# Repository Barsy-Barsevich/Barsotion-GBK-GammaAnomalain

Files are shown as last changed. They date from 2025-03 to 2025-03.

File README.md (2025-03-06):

# Barsotion GBK GammaAnomalain

Board computer created for "OKB Iva "Kilka"", 2024

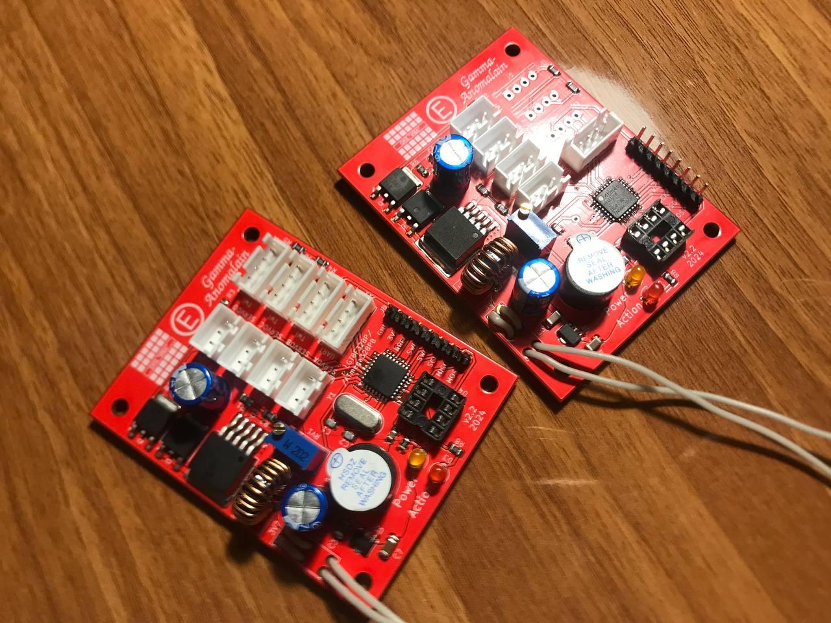
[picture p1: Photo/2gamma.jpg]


## Parameters
- Microcontroller: ATmega328PB / LGT8X328P
- Clock frequency: 16MHz / 32MHz
- Gyroscope: external, MPU6050 (I2C)
- Barometer: external, 2x BMP388 (I2C)
- Memory: 8MB SPI NOR Flash

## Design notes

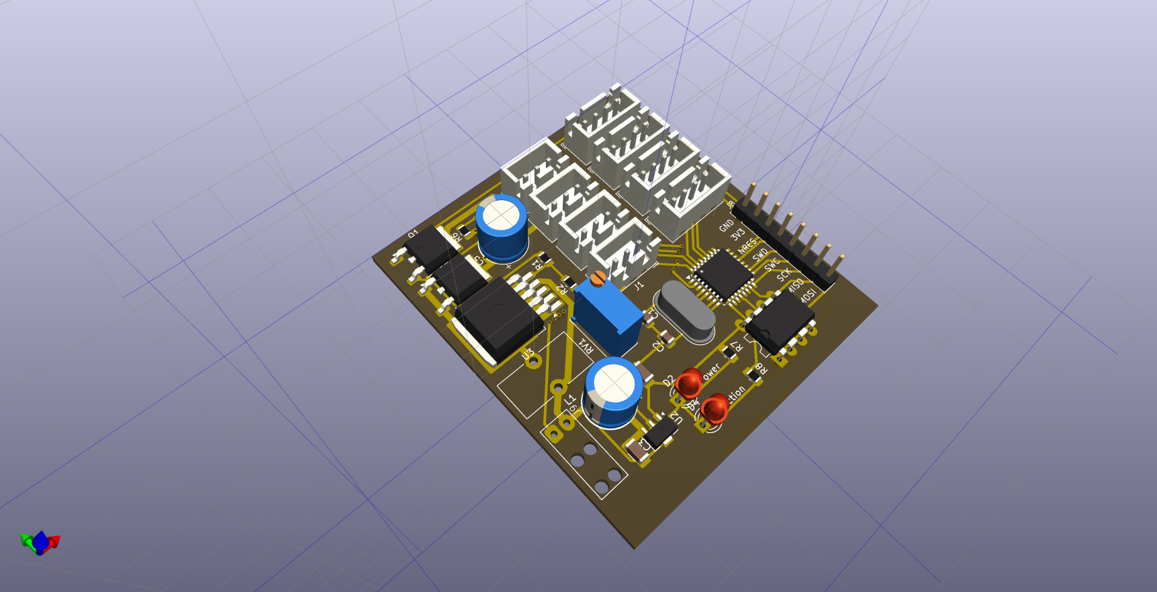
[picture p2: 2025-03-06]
Photo/GammaAnomalain.png

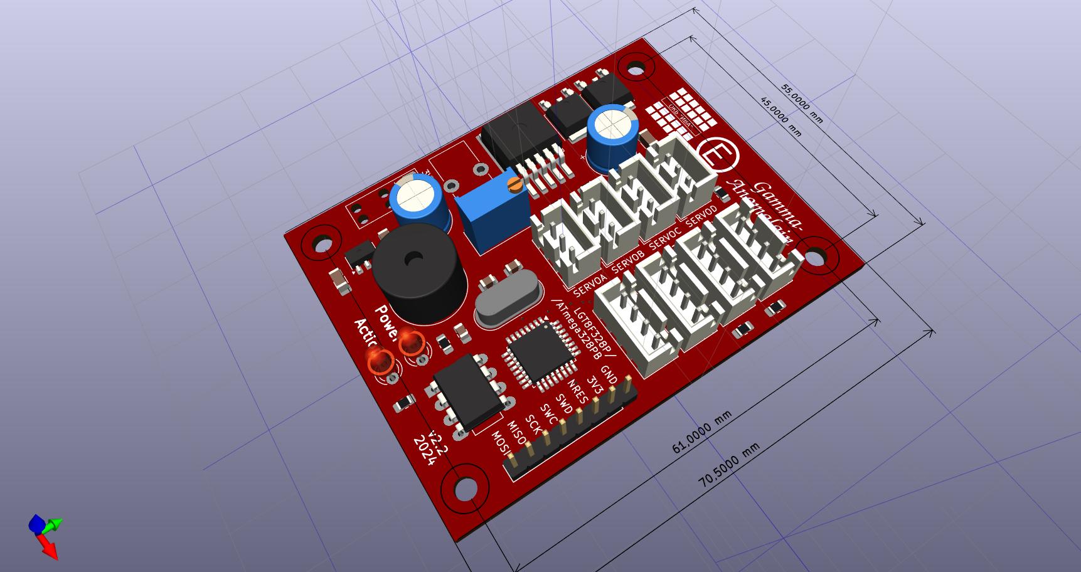
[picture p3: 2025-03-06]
Photo/GammaAnomalain_v2.2_3Dview_RedMask.jpg

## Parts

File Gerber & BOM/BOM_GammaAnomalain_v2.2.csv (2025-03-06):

Reference | Value | Footprint | Description
BZ1 | Buzzer | Buzzer_Beeper:MagneticBuzzer_ProSignal_ABI-009-RC | Buzzer, polarized
C1 | 22pF | Capacitor_SMD:C_0805_2012Metric | Unpolarized capacitor
C2 | 22pF | Capacitor_SMD:C_0805_2012Metric | Unpolarized capacitor
C3 | 1uF | Capacitor_SMD:C_1206_3216Metric_Pad1.33x1.80mm_HandSolder | Unpolarized capacitor
C4 | 470uF | Capacitor_THT:CP_Radial_D8.0mm_P3.50mm | Polarized capacitor
C5 | 470uF | Capacitor_THT:CP_Radial_D8.0mm_P3.50mm | Polarized capacitor
C6 | 1uF | Capacitor_SMD:C_1206_3216Metric_Pad1.33x1.80mm_HandSolder | Unpolarized capacitor
C7 | 1uF | Capacitor_SMD:C_1206_3216Metric_Pad1.33x1.80mm_HandSolder | Unpolarized capacitor
C8 | 10nF | Capacitor_SMD:C_0805_2012Metric_Pad1.18x1.45mm_HandSolder | Unpolarized capacitor
D1 | MBRD1045 | CustomPackage:TO-252-2_TabPin1_Other2 | Schottky Rectifier 45V 10(150)A TO252-2
D2 | LED_WORK | LED_THT:LED_D3.0mm | Light emitting diode
D3 | LED_ACTIVE | LED_THT:LED_D3.0mm | Light emitting diode
H1 | MountingHole | MountingHole:MountingHole_3.2mm_M3 | Mounting Hole without connection
H2 | MountingHole | MountingHole:MountingHole_3.2mm_M3 | Mounting Hole without connection
H3 | MountingHole | MountingHole:MountingHole_3.2mm_M3 | Mounting Hole without connection
H4 | MountingHole | MountingHole:MountingHole_3.2mm_M3 | Mounting Hole without connection
J1 | Conn_ServoA | Connector_JST:JST_XH_B3B-XH-A_1x03_P2.50mm_Vertical | Generic connector, single row, 01x03, script generated
J2 | Conn_ServoB | Connector_JST:JST_XH_B3B-XH-A_1x03_P2.50mm_Vertical | Generic connector, single row, 01x03, script generated
J3 | Conn_ServoC | Connector_JST:JST_XH_B3B-XH-A_1x03_P2.50mm_Vertical | Generic connector, single row, 01x03, script generated
J4 | Conn_ServoD | Connector_JST:JST_XH_B3B-XH-A_1x03_P2.50mm_Vertical | Generic connector, single row, 01x03, script generated
J5 | Conn_MPU | Connector_JST:JST_XH_B4B-XH-A_1x04_P2.50mm_Vertical | Generic connector, single row, 01x04, script generated
J6 | Conn_BMP0 | Connector_JST:JST_XH_B4B-XH-A_1x04_P2.50mm_Vertical | Generic connector, single row, 01x04, script generated
J7 | Conn_BMP1 | Connector_JST:JST_XH_B4B-XH-A_1x04_P2.50mm_Vertical | Generic connector, single row, 01x04, script generated
J8 | Conn_SWD | Connector_PinHeader_2.54mm:PinHeader_1x08_P2.54mm_Vertical | Generic connector, single row, 01x08, script generated
J9 | Conn_BAT | CustomConnectors:Battery_3V7_Cable_solding_connctor | Generic connector, single row, 01x02, script generated
J10 | Conn_UART | Connector_JST:JST_XH_B4B-XH-A_1x04_P2.50mm_Vertical | Generic connector, single row, 01x04, script generated
L1 | 47uh | Inductor_THT:L_Toroid_Vertical_L13.0mm_W6.5mm_P5.60mm | Inductor with ferrite core, small symbol
Q1 | IRLR8726 | Package_TO_SOT_SMD:TO-252-2 | 1.7A Id, 500V Vds, CoolMOS N-Channel Power MOSFET, 3Ohm Ron, 4.3nC Qg (typ), TO-252-2
R1 | 1k | Resistor_SMD:R_0805_2012Metric_Pad1.20x1.40mm_HandSolder | Resistor
R2 | 3k | Resistor_SMD:R_0805_2012Metric_Pad1.20x1.40mm_HandSolder | Resistor
R3 | 10k | Resistor_SMD:R_0805_2012Metric_Pad1.20x1.40mm_HandSolder | Resistor
R4 | 10k | Resistor_SMD:R_0805_2012Metric_Pad1.20x1.40mm_HandSolder | Resistor
R5 | 10k | Resistor_SMD:R_0805_2012Metric_Pad1.20x1.40mm_HandSolder | Resistor
R6 | 1k | Resistor_SMD:R_0805_2012Metric_Pad1.20x1.40mm_HandSolder | Resistor
R7 | 3.3k | Resistor_SMD:R_0805_2012Metric_Pad1.20x1.40mm_HandSolder | Resistor
R8 | 3.3k | Resistor_SMD:R_0805_2012Metric_Pad1.20x1.40mm_HandSolder | Resistor
RV1 | 1k | Potentiometer_THT:Potentiometer_Bourns_3296W_Vertical | Potentiometer
U1 | LGT8F328P | Package_QFP:LQFP-32_7x7mm_P0.8mm | 8-bit microcontroller based on AVR architecture
U2 | L78L33_SOT89 | Package_TO_SOT_SMD:SOT-89-3 | Positive 100mA 30V Linear Regulator, Fixed Output 3.3V, SOT-89
U3 | XL6019 | Package_TO_SOT_SMD:TO-263-5_TabPin3 | DC-DC Pull-up converter
U4 | W25Q128JVS | Package_DIP:DIP-8_W7.62mm_LongPads | 128Mb Serial Flash Memory, Standard/Dual/Quad SPI, SOIC-8
Y1 | Crystal | Crystal:Crystal_HC49-4H_Vertical | Two pin crystal

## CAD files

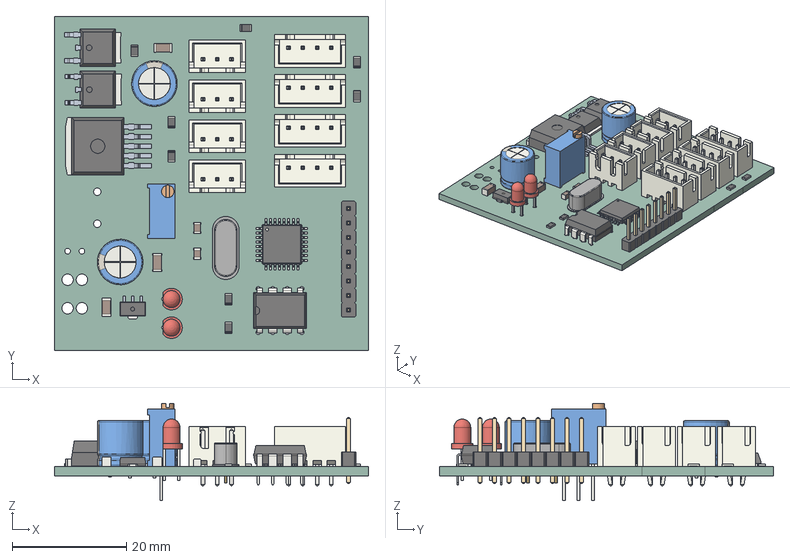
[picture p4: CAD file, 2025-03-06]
Step/GammaAnomalain.step
55.0 x 58.5 x 17.1 mm
R_0805_2012Metric x 8
CP_Radial_D80mm_P350mm x 2
C_1206_3216Metric x 3
Crystal_HC49-4H_Vertical
JST_B3B_XH_A x 4
JST_B4B_XH_A x 4
CQ assembly x 4
DIP-8_W7.62mm
C_0805_2012Metric x 2
LED_D3.0mm x 2
LQFP_32_7x7mm_P08mm
Potentiometer_Bourns_3296W_Vertical
PinHeader_1x08_P254mm_Vertical
GammaAnomalain_PCB

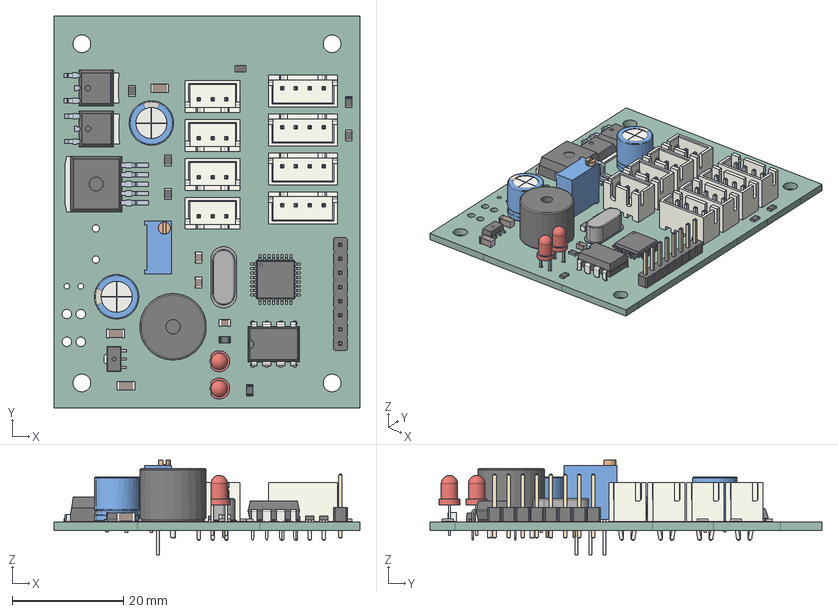
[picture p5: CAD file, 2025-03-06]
Step/GammaAnomalain_v2.2.step
55.0 x 70.5 x 17.1 mm
R_0805_2012Metric x 8
CP_Radial_D80mm_P350mm x 2
C_1206_3216Metric x 3
Crystal_HC49-4H_Vertical
JST_B3B_XH_A x 4
JST_B4B_XH_A x 4
CQ assembly x 4
DIP-8_W7.62mm
C_0805_2012Metric x 3
LED_D3.0mm x 2
MagneticBuzzer_ProSignal_ABI_009_RC
LQFP_32_7x7mm_P08mm
Potentiometer_Bourns_3296W_Vertical
PinHeader_1x08_P254mm_Vertical
GammaAnomalain_PCB

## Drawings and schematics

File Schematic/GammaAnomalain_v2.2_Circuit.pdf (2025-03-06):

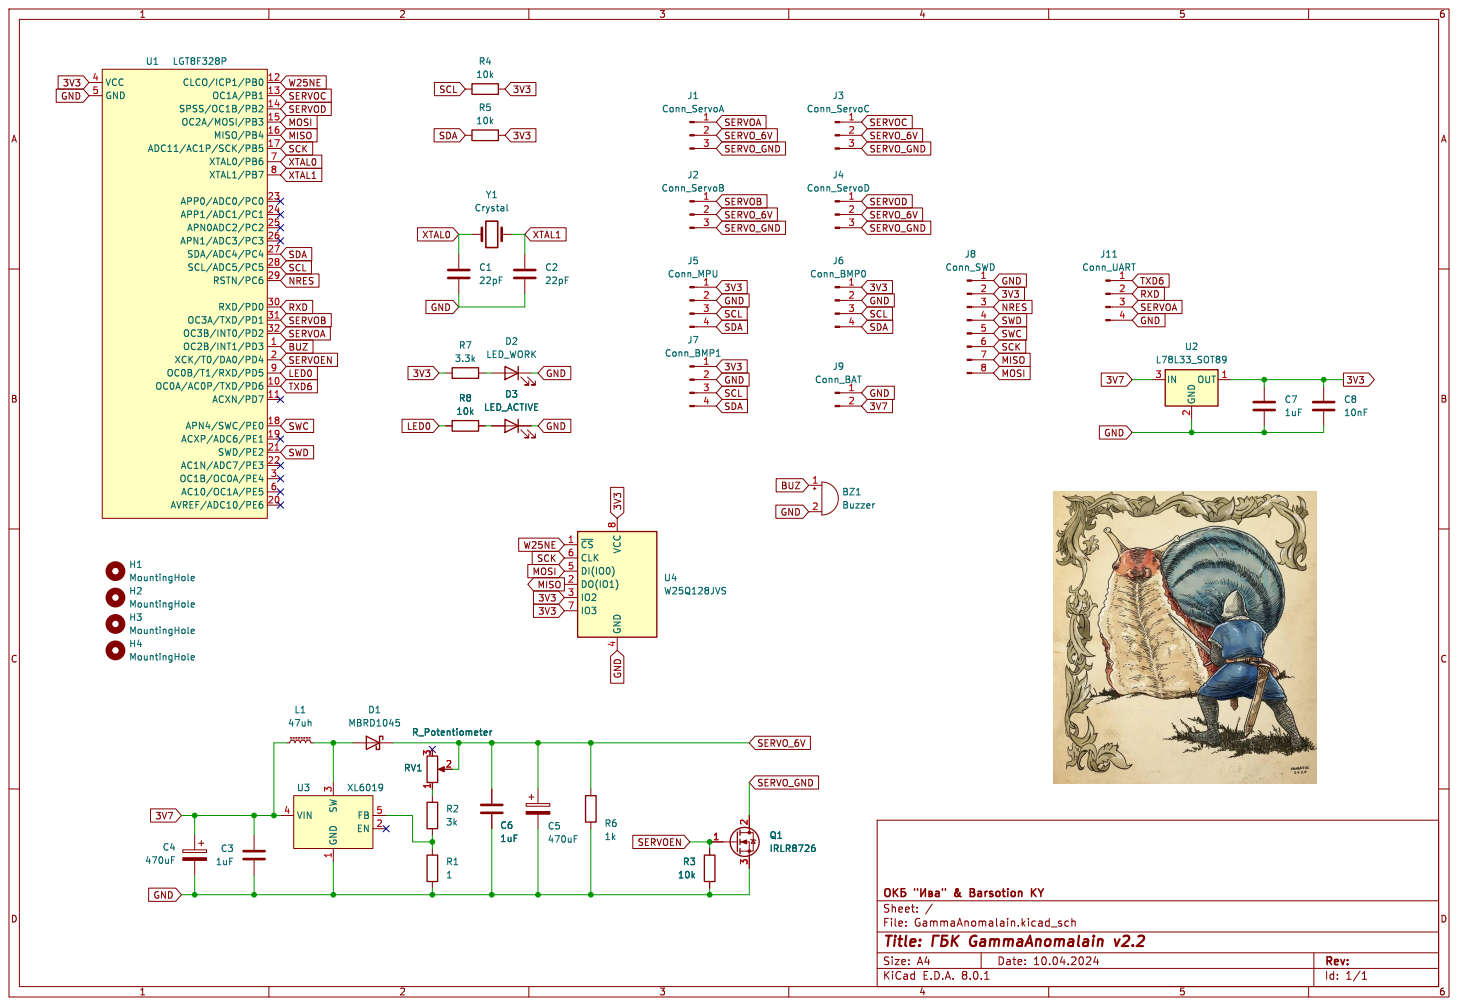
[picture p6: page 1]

SERVOD MOSI BUZ SDA

3 VIN 4 FB 5 U3 XL6019 GND MISO

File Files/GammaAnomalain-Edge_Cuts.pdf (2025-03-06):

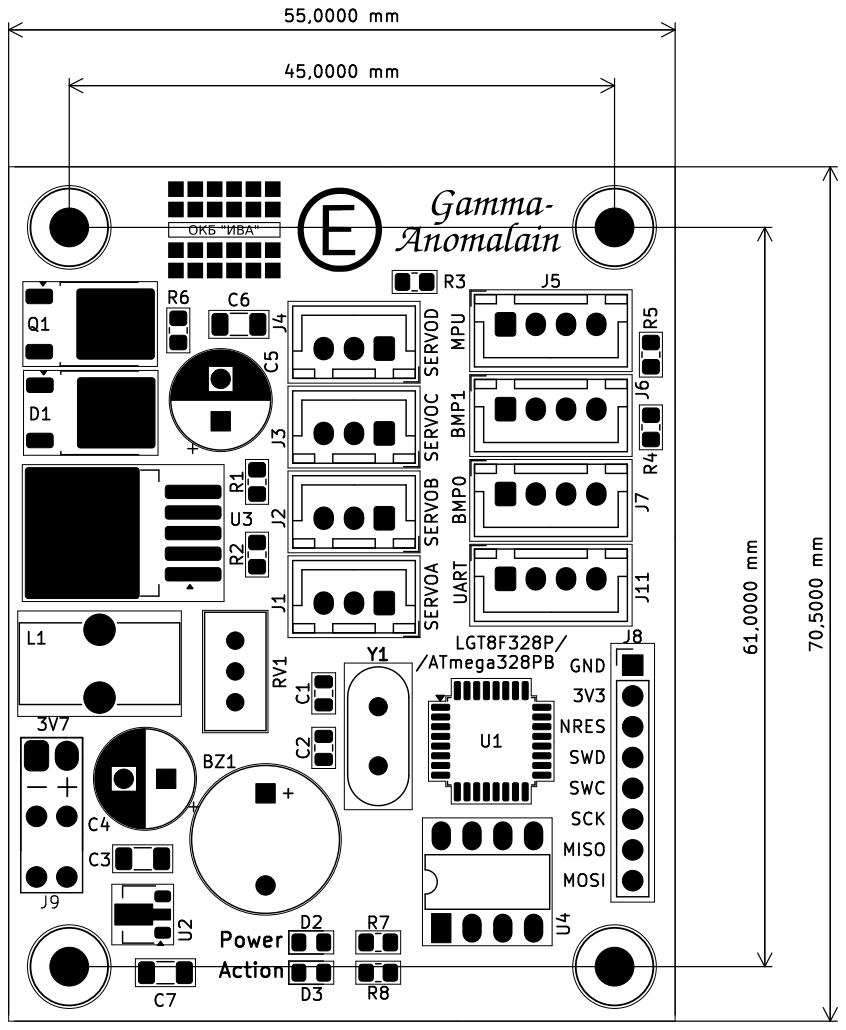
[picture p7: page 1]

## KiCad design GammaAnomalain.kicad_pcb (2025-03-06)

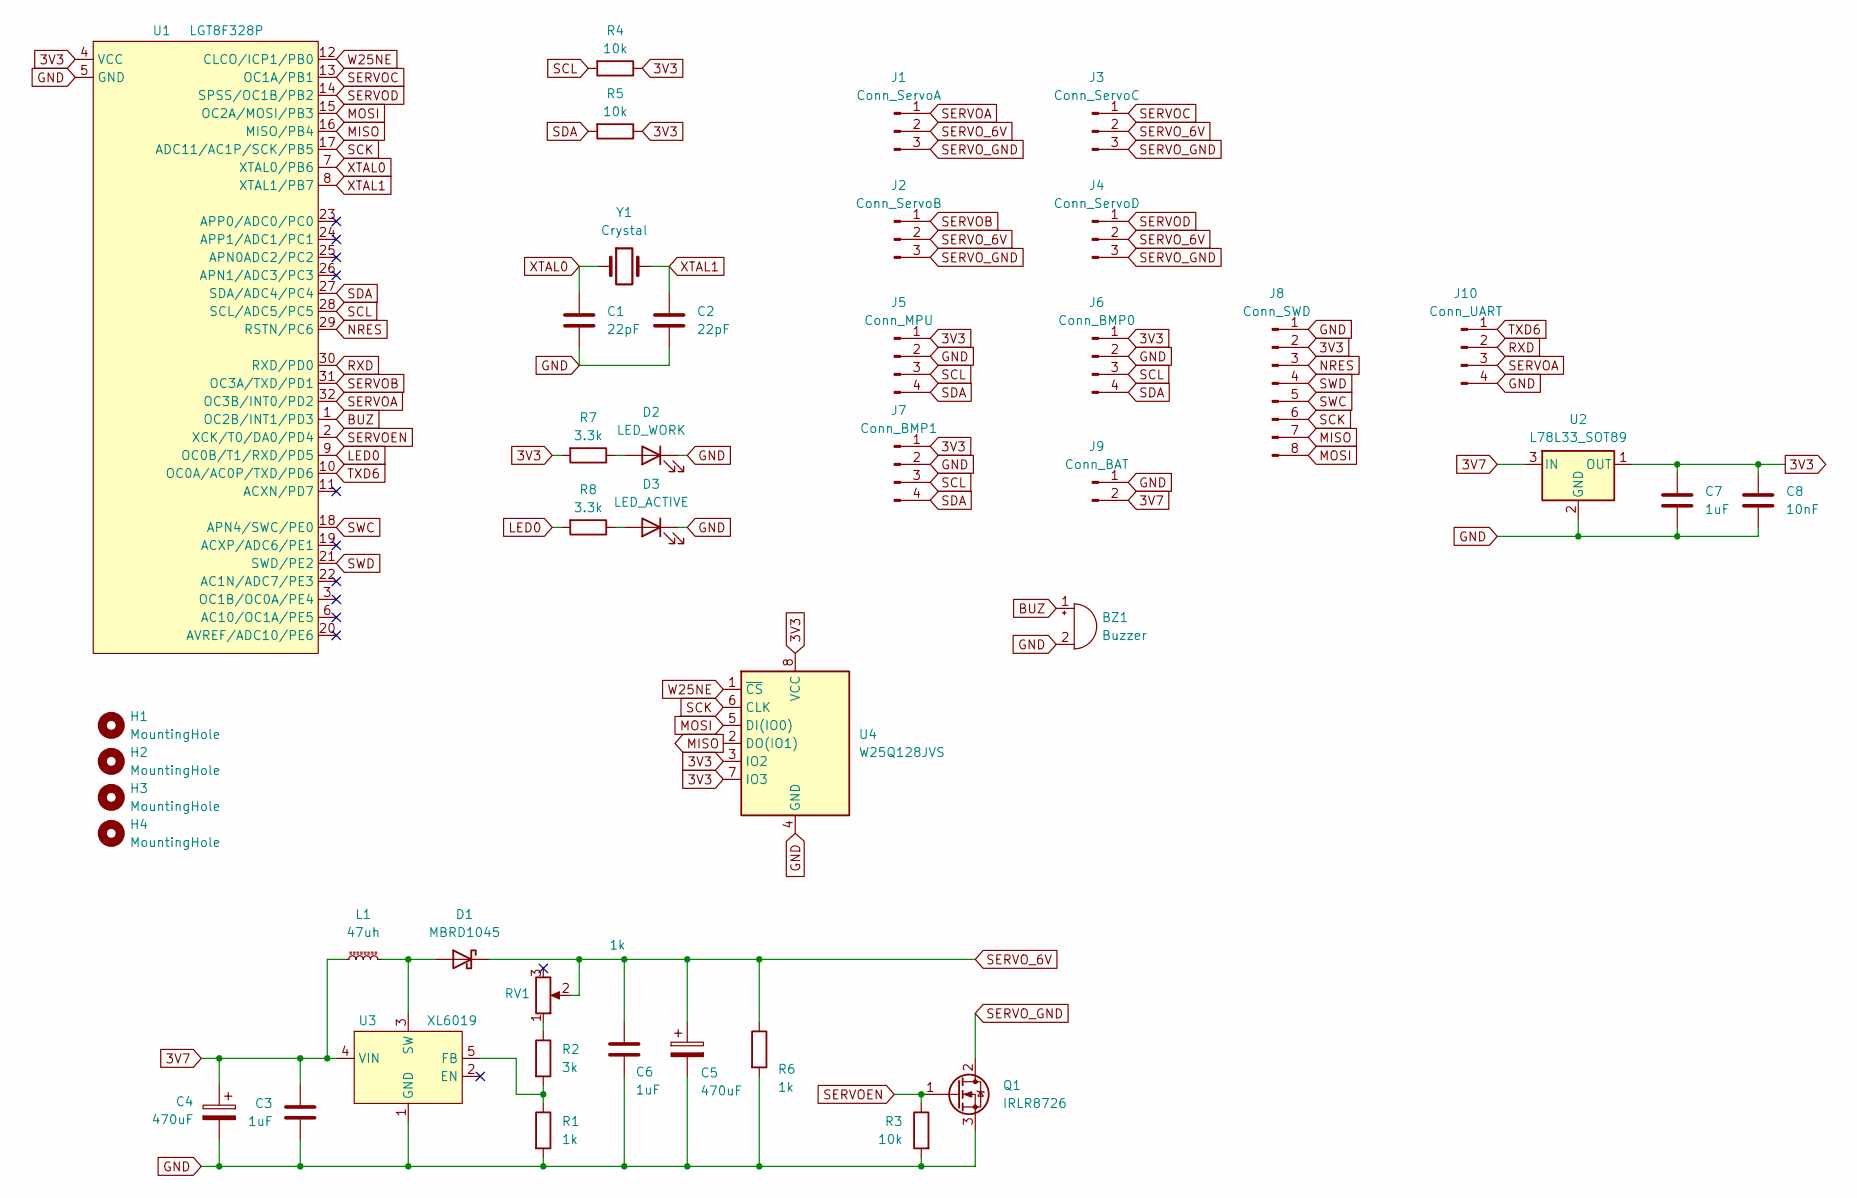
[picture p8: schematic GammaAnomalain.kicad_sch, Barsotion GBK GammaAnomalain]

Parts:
BZ1: Buzzer; MagneticBuzzer_ProSignal_ABI-009-RC
C1, C2: 22pF; C_0805_2012Metric
C3, C6, C7: 1uF; C_1206_3216Metric_Pad1.33x1.80mm_HandSolder
C4, C5: 470uF; CP_Radial_D8.0mm_P3.50mm
C8: 10nF; C_0805_2012Metric_Pad1.18x1.45mm_HandSolder
D1: MBRD1045; TO-252-2_TabPin1_Other2
D2: LED_WORK; LED_D3.0mm
D3: LED_ACTIVE; LED_D3.0mm
H1, H2, H3, H4: MountingHole; MountingHole_3.2mm_M3
J1: Conn_ServoA; JST_XH_B3B-XH-A_1x03_P2.50mm_Vertical
J2: Conn_ServoB; JST_XH_B3B-XH-A_1x03_P2.50mm_Vertical
J3: Conn_ServoC; JST_XH_B3B-XH-A_1x03_P2.50mm_Vertical
J4: Conn_ServoD; JST_XH_B3B-XH-A_1x03_P2.50mm_Vertical
J5: Conn_MPU; JST_XH_B4B-XH-A_1x04_P2.50mm_Vertical
J6: Conn_BMP0; JST_XH_B4B-XH-A_1x04_P2.50mm_Vertical
J7: Conn_BMP1; JST_XH_B4B-XH-A_1x04_P2.50mm_Vertical
J8: Conn_SWD; PinHeader_1x08_P2.54mm_Vertical
J9: Conn_BAT; Battery_3V7_Cable_solding_connctor
J10: Conn_UART; JST_XH_B4B-XH-A_1x04_P2.50mm_Vertical
L1: 47uh; L_Toroid_Vertical_L13.0mm_W6.5mm_P5.60mm
Q1: IRLR8726; TO-252-2
R1, R6: 1k; R_0805_2012Metric_Pad1.20x1.40mm_HandSolder
R2: 3k; R_0805_2012Metric_Pad1.20x1.40mm_HandSolder
R3, R4, R5: 10k; R_0805_2012Metric_Pad1.20x1.40mm_HandSolder
R7, R8: 3.3k; R_0805_2012Metric_Pad1.20x1.40mm_HandSolder
RV1: 1k; Potentiometer_Bourns_3296W_Vertical
U1: LGT8F328P; LQFP-32_7x7mm_P0.8mm
U2: L78L33_SOT89; SOT-89-3
U3: XL6019; TO-263-5_TabPin3
U4: W25Q128JVS; DIP-8_W7.62mm_LongPads
Y1: Crystal; Crystal_HC49-4H_Vertical

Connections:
3V3: C7.1, C8.1, J5.1, J6.1, J7.1, J8.2, R4.1, R5.1, R7.2, U1.4 (VCC), U2.1 (OUT), U4.3 (IO2), U4.7 (IO3), U4.8 (VCC)
3V7: C3.1, C4.1, J9.2, L1.1, U2.3 (IN), U3.4 (VIN)
BUZ: BZ1.1 (+), U1.1 (OC2B/INT1/PD3)
GND: BZ1.2 (-), C1.2, C2.2, C3.2, C4.2, C5.2, C6.2, C7.2, C8.2, D2.1 (K), D3.1 (K), J5.2, J6.2, J7.2, J8.1, J9.1, J10.4, Q1.3 (S), R1.2, R3.2, R6.2, U1.5 (GND), U2.2 (GND), U3.1 (GND), U4.4 (GND); also elsewhere on the board
LED0: R8.2, U1.9 (OC0B/T1/RXD/PD5)
MISO: J8.7, U1.16 (MISO/PB4), U4.2 (DO(IO1))
MOSI: J8.8, U1.15 (OC2A/MOSI/PB3), U4.5 (DI(IO0))
NRES: J8.3, U1.29 (RSTN/PC6)
unnamed: D1.2 (A), L1.2, U3.3 (SW)
unnamed: D2.2 (A), R7.1
unnamed: D3.2 (A), R8.1
unnamed: R2.1, RV1.1
unnamed: R1.1, R2.2, U3.5 (FB)
RXD: J10.2, U1.30 (RXD/PD0); also elsewhere on the board
SCK: J8.6, U1.17 (ADC11/AC1P/SCK/PB5), U4.6 (CLK)
SCL: J5.3, J6.3, J7.3, R4.2, U1.28 (SCL/ADC5/PC5)
SDA: J5.4, J6.4, J7.4, R5.2, U1.27 (SDA/ADC4/PC4)
SERVOA: J1.1, J10.3, U1.32 (OC3B/INT0/PD2); also elsewhere on the board
SERVOB: J2.1, U1.31 (OC3A/TXD/PD1)
SERVOC: J3.1, U1.13 (OC1A/PB1)
SERVOD: J4.1, U1.14 (SPSS/OC1B/PB2)
SERVOEN: Q1.1 (G), R3.1, U1.2 (XCK/T0/DA0/PD4)
SERVO_6V: C5.1, C6.1, D1.1 (K), J1.2, J2.2, J3.2, J4.2, R6.1, RV1.2
SERVO_GND: J1.3, J2.3, J3.3, J4.3, Q1.2 (D)
SWC: J8.5, U1.18 (APN4/SWC/PE0)
SWD: J8.4, U1.21 (SWD/PE2)
TXD6: J10.1, U1.10 (OC0A/AC0P/TXD/PD6); also elsewhere on the board
W25NE: U1.12 (CLCO/ICP1/PB0), U4.1 (~CS)
XTAL0: C1.1, U1.7 (XTAL0/PB6), Y1.1
XTAL1: C2.1, U1.8 (XTAL1/PB7), Y1.2

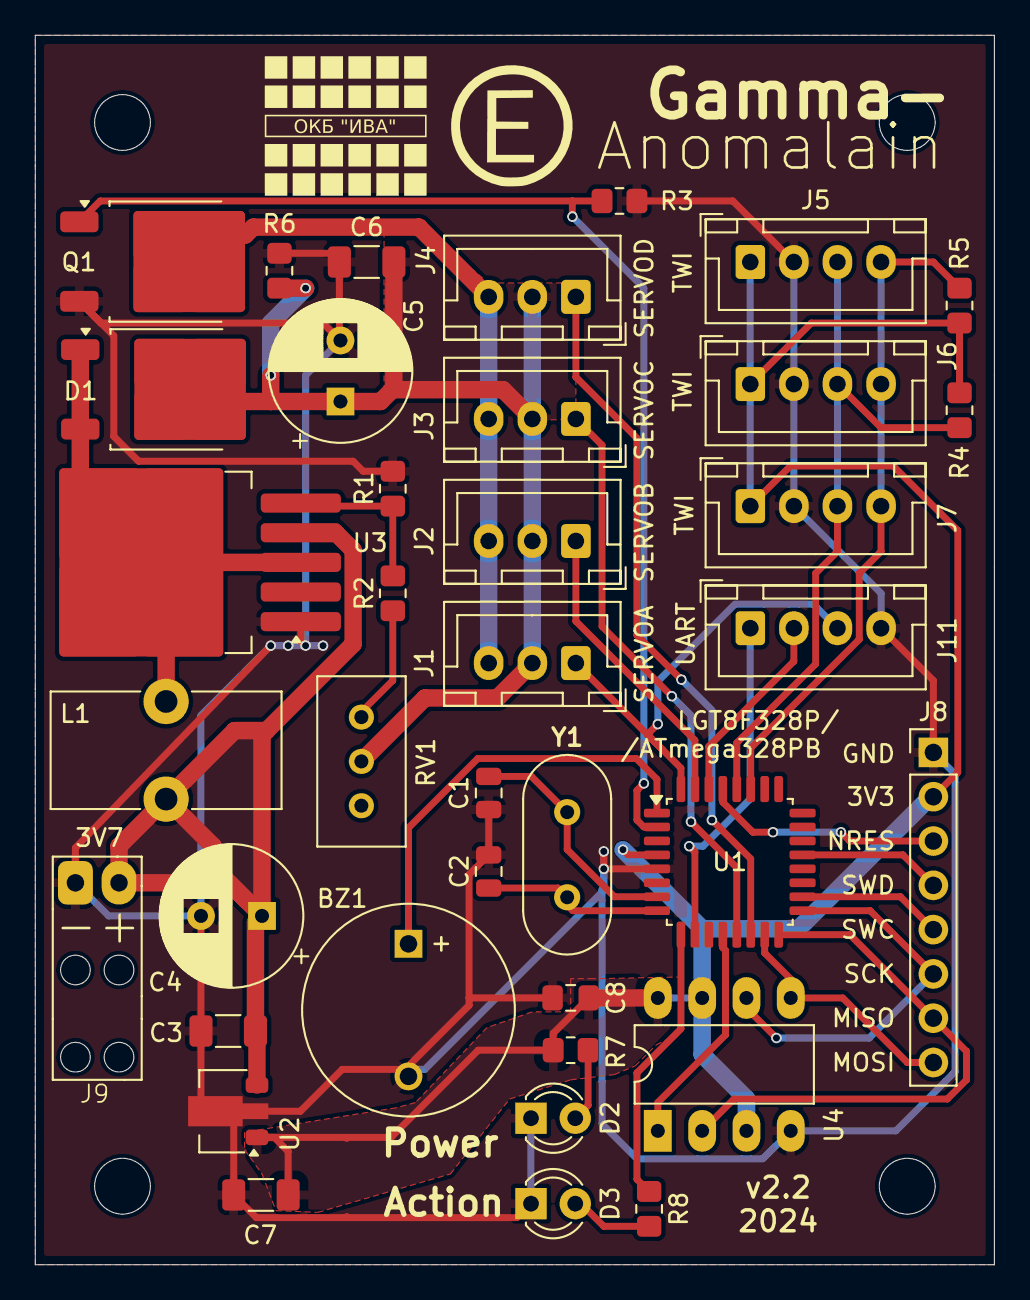
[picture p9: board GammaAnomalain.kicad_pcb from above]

Board: 2 copper layers, 55.0 x 70.5 mm, 42 parts (0 on the bottom side), 30 nets.

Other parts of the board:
J11: Conn_UART; JST_XH_B4B-XH-A_1x04_P2.50mm_Vertical

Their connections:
GND: J11.4; also elsewhere on the board
RXD: J11.2; also elsewhere on the board
SERVOA: J11.3; also elsewhere on the board
TXD6: J11.1; also elsewhere on the board
